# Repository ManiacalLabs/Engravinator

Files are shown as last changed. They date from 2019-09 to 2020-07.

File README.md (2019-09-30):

# Engravinator

The Engravinator is an Open Hardware laser engraver platform, designed to be robust and easy to build. It uses a combination of aluminum extrusions, commodity parts easily sourced from the 3D printer world, and 3D printed parts.

Unlike most laser engravers, however, it is designed to be brought to the work piece, not the other way around. It's compact and lightweight frame allows it to easily be rested, or even clamped, onto nearly any item you want to engrave.

Its existence is two-fold: To be both a fully functional laser engraver platform as designed *and* to be a highly flexible reference platform for other open designs.

For full details go to https://Engravinator.com

# Mk1 Specs

- 130mm x 130mm working area
- 345mm x 305mm x 245mm (W x D x H) overall size
- Under 4kg total weight at full spec
- Supports common PWM diode laser modules with a 16mm x 40mm M3 mounting pattern
- Up to 10,000 mm/min on X and 6,000 mm/min on Y travel speed
- 10 micron resolution (using 1/16 micro-stepping)
- 8mm linear rods and bearings on both axis
- Rigid 2020 aluminum extrusion frame
- Optional (but recommended!) full enclosure for maximum eye safety

# Design & License

As with all things from Maniacal Labs, the Engravinator is open hardware and is licensed under the [CERN Open Hardware License](/LICENSE).

You can find a complete [Fusion 360 archive](/Mk1/Engravinator.f3z) which contains the full design and all design history.

The [Fabrication](/Mk1/Fabrication/) directory contains a full set of exported files for everything you need to build the machine. For 3D Printed components we provide both `STL` files for printing and `STEP` files in case you would like to make modifications to a single model outside of the complete design, or in a different CAD tool.

# Mandatory Safety & Legal Warning

**Lasers are dangerous!** Seriously, we cannot stress enough that any laser, even low power lasers, if used improperly, can cause severe damage or injury. Use common sense and always use proper safety equipment.

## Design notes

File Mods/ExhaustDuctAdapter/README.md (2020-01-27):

# 4-Inch Exhaust Duct Adapter

Is the 80mm exhaust fan and carbon filter just not cutting it? No worries, just print this 4-inch duct adapter and vent outside!

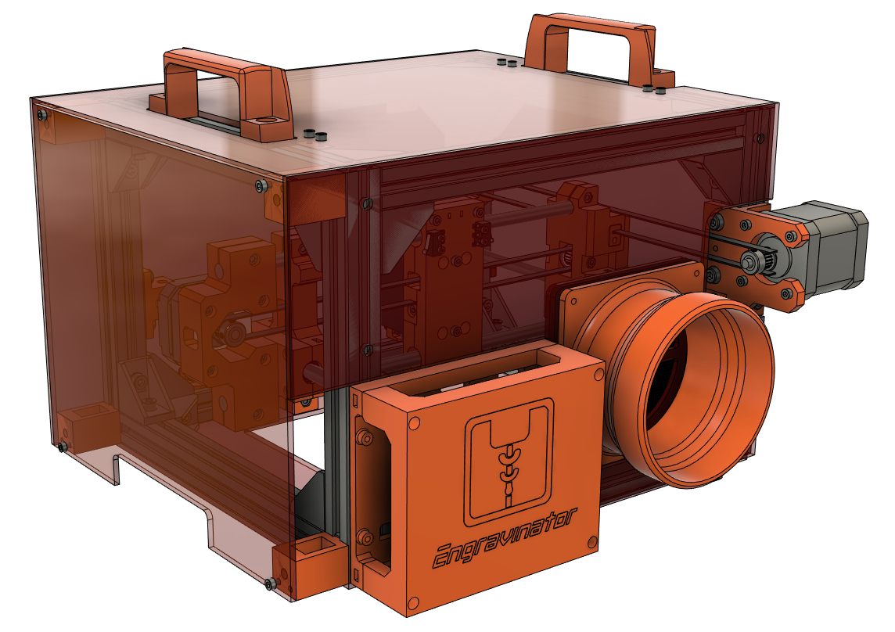
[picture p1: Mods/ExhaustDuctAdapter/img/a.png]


## Required Components

- Duct Adapter Printed Part - [4InchDuctAdapter.stl](4InchDuctAdapter.stl)
- 4x M3x10 bolts
- 4x M3 Nuts
- 4-inch flexible ducting
- 4-inch exhaust blower fan

## Assembly

- Print [4InchDuctAdapter.stl](4InchDuctAdapter.stl). We recommend 0.2mm layer heights with 20% infill. But it doesn't really matter.
- Remove the back panel from your Engravinator if it was already installed and remove the fan and filter holder.
- Use the M3x10 bolts and M3 nuts to mount the duct adapter to your Engravinator.
- Remount the back panel.

What, you were expecting more?

The rest is really up to you. We've had good luck with a generic 200CFM exhaust blower found on Amazon. Anything that's for a 4-inch duct hose will work. Connect one length of duct from the Engravinator to the blower (ideally using duct clamps but tape works too) then another length from the exhaust end of the blower to wherever you want to vent. Out a window works well.

If you are really stuck with no outside venting options we recommend using a large carbon filter canister such as this one: https://www.amazon.com/gp/product/B07B3RNW35/

This filter canister setup was used with great success for 2 solid days at ERRF 2019 with no complaints from anyone about fumes or smoke.

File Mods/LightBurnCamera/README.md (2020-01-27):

# LightBurn Camera

LightBurn has this [awesome feature](https://github.com/LightBurnSoftware/Documentation/blob/master/Using_a_Camera.md) that allows you to accurately place your designs using a calibrated camera view. Follow bellow to find out how to install a compatible camera on your Engravinator!

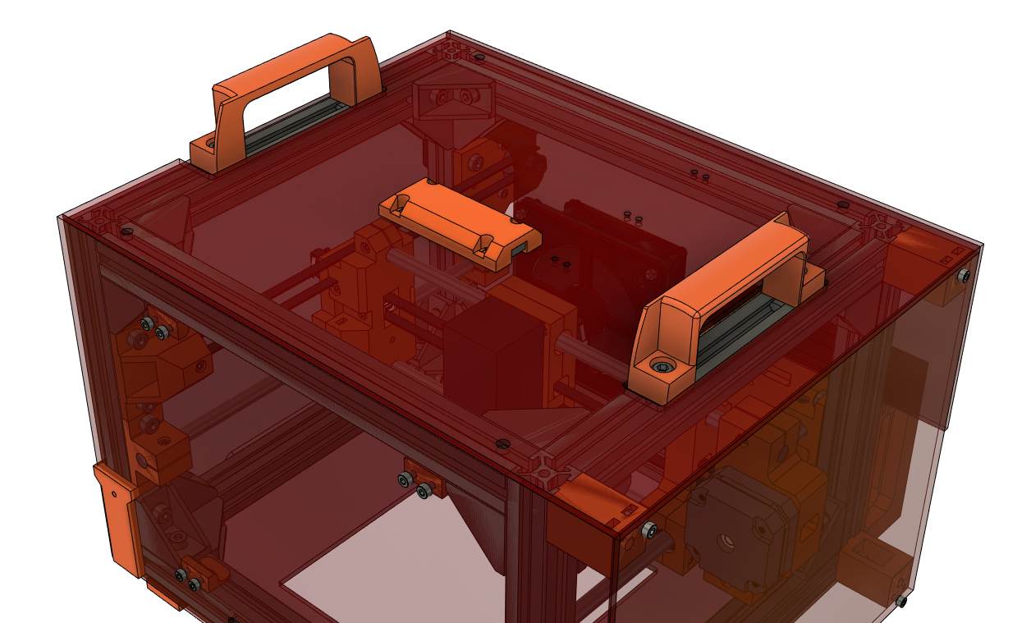
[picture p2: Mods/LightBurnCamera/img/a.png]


## Required Components

- Camera Mount (3D Printed) - [LightBurnCameraMount.stl](LightBurnCameraMount.stl)
- New top panel, cut from [TopPanel_LightBurnCamera.dxf](TopPanel_LightBurnCamera.dxf)  in 3mm 2422 Amber acrylic.
- [LightBurn Camera 90&deg;](https://lightburnsoftware.com/collections/cameras/products/lightburn-camera?variant=13886769922093)
- 2x M1.7x3mm Screws (or just use hot glue)
- 4x M3x10 bolts
- 4x M3 Nuts
- 4x M5x10 bolts
- 4x [HNTP5-5](https://us.misumi-ec.com/vona2/detail/110302247640/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) Spring nuts
- Small zip ties

## Assembly

This one is pretty simple:

- Before anything, there is a small dab of glue holding the camera lens at a specific focus. Pick that off with some small tweezers so we can focus it later.
- Print the camera mount listed above. 0.2mm layer heights, 20% infill.
- Mount the LightBurn camera in it with the M1.7 screws or, honestly, just use a couple dabs of hot glue. Those screws are a pain to find.
- Mount the camera mount to the new top acrylic panel using the M3x10 bolts and M3 nuts. See picture above for orientation.
- Connect the USB cable to the camera and hold it down using the 3 other sets of holes in the top panel and some zip ties.
- Mount the top panel to the frame using the M5x10 bolts and HNTP5-5 extrusion spring nuts. The top panel MUST be firmly mounted and not be allowed to shift at all.

That's it, not it just needs to be setup with LightBurn. All of the LightBurn camera docs can be found here: https://github.com/LightBurnSoftware/Documentation/blob/master/Using_a_Camera.md

One thing of note is that the lens calibration step requires a calibration pattern to be printed out and placed various places inside the machine. But it was never intended for a machine this small. We recommend printing out the calibration pattern at 25% size and then taping it to a small piece of stiff cardboard, roughly the size of a business card.

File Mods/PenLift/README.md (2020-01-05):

# Pen Lift Mechanism

So, maybe lasers aren't your thing and you prefer ink? Just install this pen lift mechanism that is a drop in replacement for the laser module :)

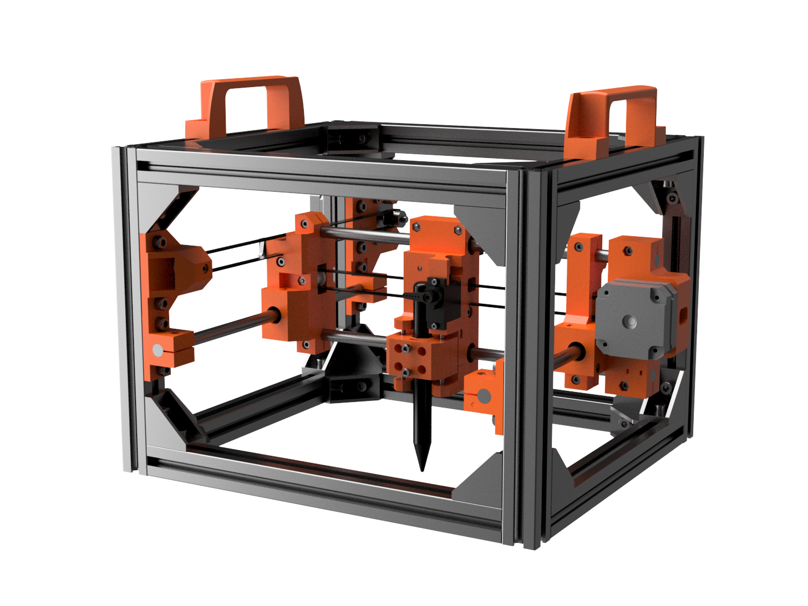
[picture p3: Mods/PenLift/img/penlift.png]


## Required Components

- Printed Components (Use [PenLiftPrintPlate.stl](Printed_Parts/PenLiftPrintPlate.stl))
- [9g Micro Servo](https://www.amazon.com/gp/product/B07NV476P7/)
- 4x [LMU3 Bearings](https://us.misumi-ec.com/vona2/detail/110300026540/?HissuCode=LMU3)
- 2x [3mm Diameter x 40mm linear rod](https://us.misumi-ec.com/vona2/detail/110302634310/?HissuCode=PSFJ3-40)
- 12x M3 Nut (See Engraviator [BOM Guide](https://engravinator.com/mk1/BOM_Guide.html))
- 2x [M3x10 Bolt](https://us.misumi-ec.com/vona2/detail/221000551286/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)
- 2x [M2x8 Bolt](https://us.misumi-ec.com/vona2/detail/221000551286/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)
- 6x [M3x15 Bolt](https://us.misumi-ec.com/vona2/detail/221000551286/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) (4 more will be reused from laser mount)
- Thin wire or fishing line
- Pen up to 12mm in diameter

## Assembly

This one is pretty simple, so in lieu of the full step-by-step we'll provide this annotated and exploded view of the entire assembly.

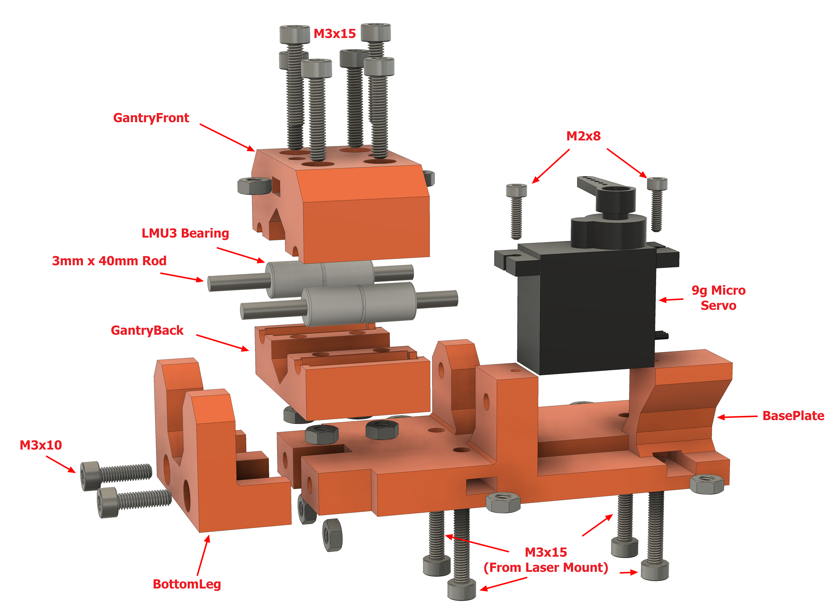
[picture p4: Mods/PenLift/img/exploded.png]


The basic steps are:

- Sandwich the four LMU3 bearings between `GantryFront` and `GantryBack`, then secure with four each of the M3x15 bolts and the M3 nuts. On GantryFront this is the 4 outer holes.
- Slide each of the 3mm rods into the bearings and then press the rods into the recessed holes on `BasePlate`.
- Take `BottomLeg` and match up the other ends of the rods with its recessed holes while lining it up with `BasePlate` and push them together as much as possible.
- Now insert two M3 nuts into the slots on the back of `BasePlate` and then two M3x10 bolts through the bottom of `BottomLeg` and tighten against those nuts. This will pull everything together and fully seat the 3mm rods.
- In `GantryFront` there are two slots for M3 nuts. Insert a nut into each and then thread in an M3x15 bolt from the top for each. These are to hold onto the pen, so do not tighten all the way yet.
- Use the M2x8 bolts to secure the micro servo.
- We recommend installing a single servo arm as shown. We will discuss connecting this to the gantry in the usage details below.

## Mounting

The pen lift mechanism goes in place of the laser.

- Simply undo the four M3x15 bolts on the back of the X-axis laser mount but leave the bolts in place. Just remove the laser. 
- Then insert an M3 nut into each of the 4 slots on the side of `BasePlate`.
- Mount the pen lift on the X-axis, matching up the holes with those M3x15 bolts. Tighten all bolts to secure.
- Finally you will need to run the servo cable in place of (or along side) the laser cable back to the controller. See the [Controller section](https://engravinator.com/mk1/build/06.Controller.html) of the build guide for more details on wiring.

## Firmware

Unfortunately it's not possible to just use stock Grbl to control a servo. There are two types of modified Grbl to control this mechanism. One controls the servo with the laser power commands and the other controls the servo as a virtual Z axis. We will be only discussing the former here. You can find firmware that uses the latter on this [GitHub repo])(https://github.com/bdring/Grbl_Pen_Servo).

However, for the Engravinator we recommend you use the firmware that we have created, which is been thoroughly tested and will be detailed here. Note: we will be assuming you are using the [Platypus](https://maniacallabs.com/products/platypus/) controller below.

First, follow the instructions here: https://github.com/ManiacalLabs/grbl/tree/builds
And install the firmware called `m3_servo`:

- [Precompiled Hex](https://github.com/ManiacalLabs/grbl/tree/builds/release/m3_servo)
- [Source](https://github.com/ManiacalLabs/grbl/tree/builds/code/m3_servo)

You will then need to change a few config items. Enter these commands (without the comment) in your controller serial terminal.

- Disable laser mode `$32=0`
- Decrease default X speed: `$110=2000.000`
- Decrease default Y speed: `$111=2000.000`

You **MUST** disable laser mode, otherwise it will move with the pen down when it shouldn't. The last two are optional but you really don't want to be going fast with a pen. This will limit it for you.

That's it, your controller is ready to rock a servo!

## Pen Setup

Almost there, we promise! The first thing we need to do is get the pen installed and hook up the servo to the gantry. 

With your Engravinator on, connected to your control software of choice, and homed: open your serial terminal and enter: 

`M3 S0`

This will move the servo to the "neutral position". At this point, make sure the servo arm is pointing to "9 o'clock" as shown in the picture below: 

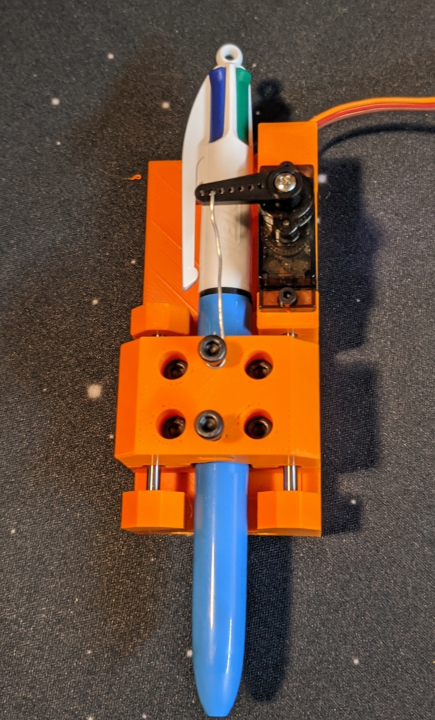
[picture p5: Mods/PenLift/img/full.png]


If the arm is not in that position, unscrew it and move it to the correct position before screwing it in again.
With the arm there, take either a piece of ~22 gauge wire (without the insulation) or some fishing line and connect it between the servo arm and the top bolt as shown above. Using fishing line will provide no downward pressure whereas a wire will provide a little. We prefer the wire because it will also bend a bit if the servo moves down too far and basically "auto adjust".

Now, enter the command:

`M3 S250`

This will move the arm to about 1/4 of full. You might think you'd want to fully extend it but that's not the case. Ideally the pen should only move up and down a tiny amount, which allows you to spend less time deploying and stowing the pen.

Now, loosen the two bolts in the center of the gantry and insert your pen of choice from the top (without the cap of course). Let it simply rest on the surface below your Engravinator. Tighten both bolts so that it holds the pen securely.

Now enter `M5` in the terminal to "stow" the pen.

## Control

This will be a little different depending on what software you choose. But no matter what you'll need to ensure that you have it program in a delay for every `M3` (pen down) command. The easiest way to do this is with the `G4` (dwell) command.

Some programs, such as LaserWeb will allow you to set "Tool On" and "Tool Off" commands. In this case, you would use:

```
; tool on
M3 S250
G4 P250

; tool off
M5
G4 P100
```

Note that the `Sxxx` value must be whatever you used above to setup your pen. Because that's where your pen is touching the paper.

The `G4 Pxxx` values are a delay where the number is milliseconds. In our testing we've found that 250ms is usually enough to make sure the pen is fully deployed and 100ms is enough to ensure it's no longer touching the surface before moving again.

These values will change depending on your particular usage. For example, if you notice that it's skipping part of a line after deploying the pen, increase the tool on delay. Or if you see that it's drawing after it should've stopped, increase the tool off delay. The idea is to have those values be as small as possible, as to not waste time.

That's pretty much it, assuming your software let's you override tool on / tool off or otherwise set delays. Now you can use it just like you would for a laser.

## LightBurn

We really love [LightBurn](https://lightburnsoftware.com) here at Maniacal Labs for all our lasering needs, but for pen use it requires a few tweaks. Mainly this is because there's currently no way to override the tool on/off commands as described above. But no worries, it's an easy fix.

First, you need to make sure that it won't use M4 power commands which means using a different GRBL profile than then one described in the [Platypus LightBurn docs](https://github.com/ManiacalLabs/Platypus/blob/master/docs/LightBurn.md). At this point we recommend creating a completely new profile to be used with the pen lift. Follow those LightBurn docs for the Platypus but when it asks you to choose a laser type, choose `GRBL-M3 (1.1e or earlier)`:

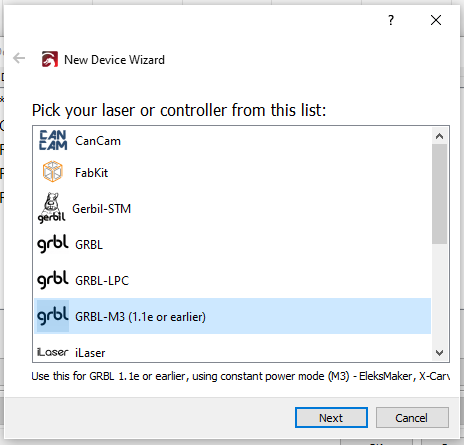
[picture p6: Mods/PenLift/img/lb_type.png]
lightburn type


Follow the rest of the Platypus docs and use all the same options otherwise. Now you just need to ensure there's a delay on pen down/up. In your cut settings you need to enable the "Cut Through" mode, as shown below:

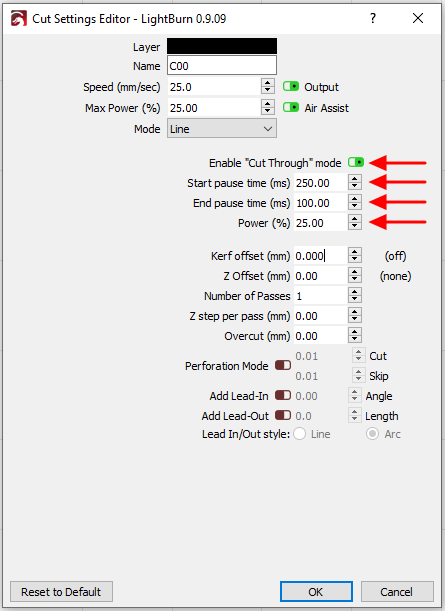
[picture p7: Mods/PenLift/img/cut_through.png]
Cut Through


The four annotated items are what's imported. 

- "Cut Through" must be turned on
- "Start pause time" is the delay on pen down
- "End pause time" is the delay on pen up
- "Power" should always be whatever "Max Power" at the top of the dialog is set to. Unfortunately you always have to set both and make sure they are the same.

Since power is in percent in LightBurn, note that 25% here is the same as `S250` above, assuming that your power range is configured for 0-1000 in Grbl (the default).

One thing we've found is that you can increase the power setting a little bit from what you used when installing the pen to provide a little more pressure (assuming you used wire instead of fishing line). So, for example, set it to 30% when the pen was installed at 25%.

That's it! You should be good to go with LightBurn.

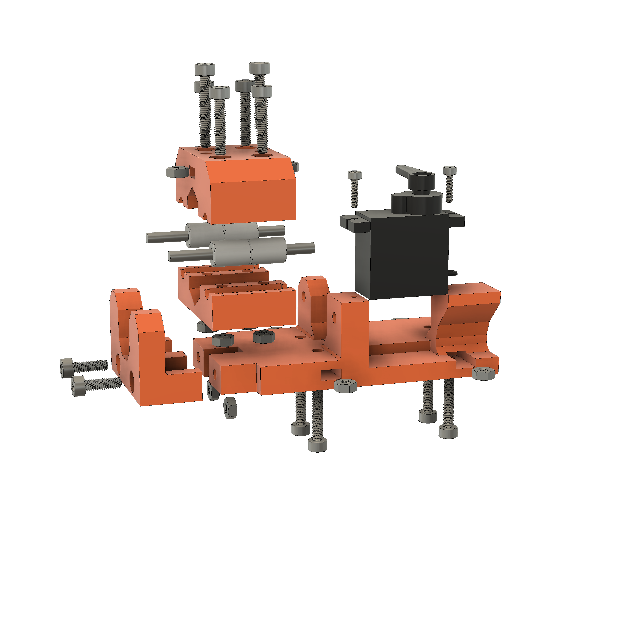
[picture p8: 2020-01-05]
Mods/PenLift/img/a.png

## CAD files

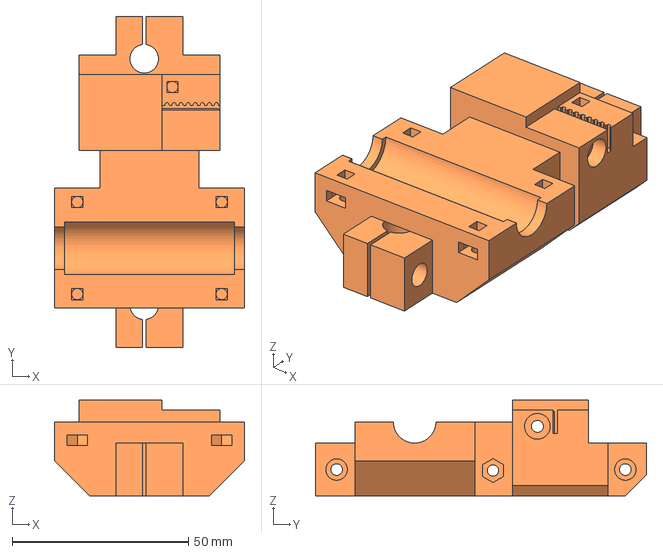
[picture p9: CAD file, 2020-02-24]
Mk1/Fabrication/3D_Printed/Core_Components/Y_Drive_Main.step
54.0 x 94.0 x 27.2 mm

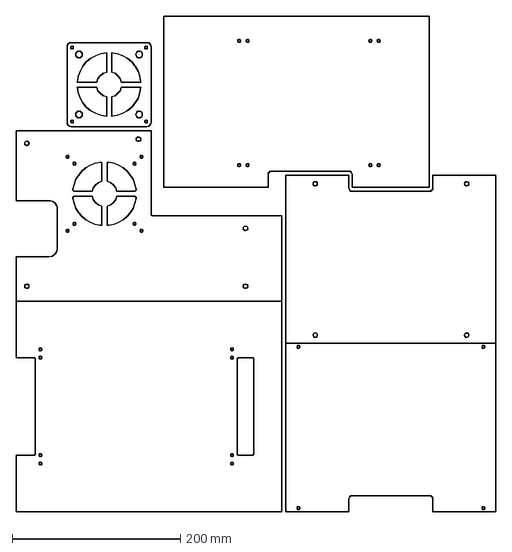
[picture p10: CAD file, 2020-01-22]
Mk1/Fabrication/Laser_Cut/ProductionFiles/FullPanelCut_SharedBorders.dxf
571.0 x 589.0 mm

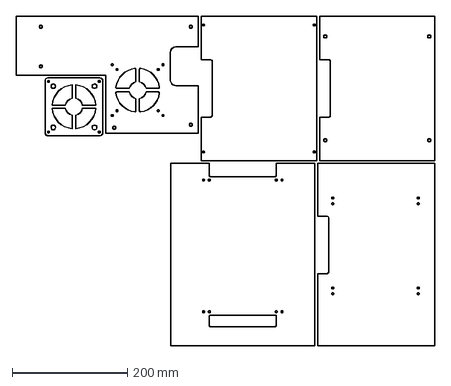
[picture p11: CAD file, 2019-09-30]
Mk1/Fabrication/Laser_Cut/FullPanelCut.dxf
726.0 x 571.0 mm

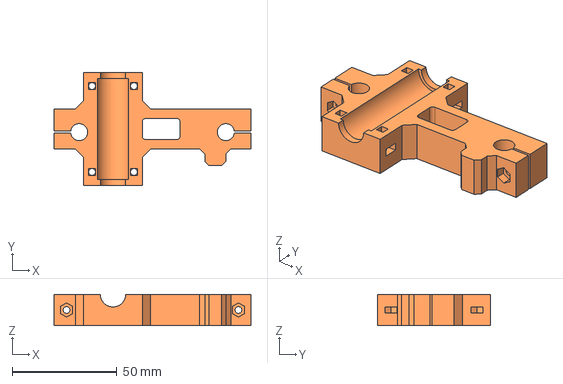
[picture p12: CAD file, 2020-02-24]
Mk1/Fabrication/3D_Printed/Core_Components/Y_Idle_Main.step
94.0 x 54.0 x 15.0 mm

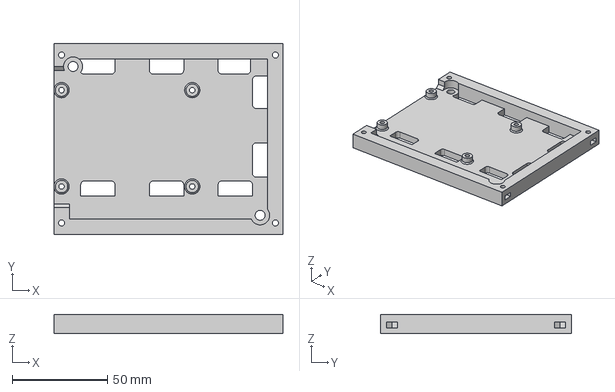
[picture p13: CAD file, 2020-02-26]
Mk1/Fabrication/3D_Printed/Controller_Box/BasePlate_Platypus.step
120.0 x 100.0 x 10.0 mm

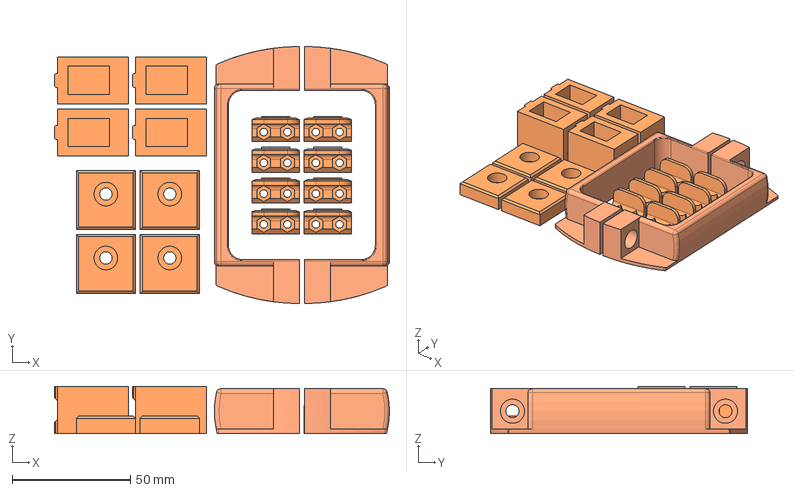
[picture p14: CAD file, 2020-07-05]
Mk1/Fabrication/3D_Printed/Enclosure/EnclosurePrintPlate.step
141.5 x 108.5 x 20.0 mm
x2_Handles x 2
x4_Feet x 4
x4_ExtensionBracket x 4
x8_PanelClips x 8

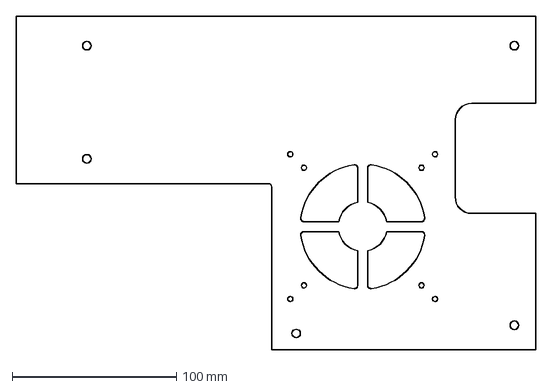
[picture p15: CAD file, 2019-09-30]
Mk1/Fabrication/Laser_Cut/BackPanel.dxf
316.0 x 203.0 mm

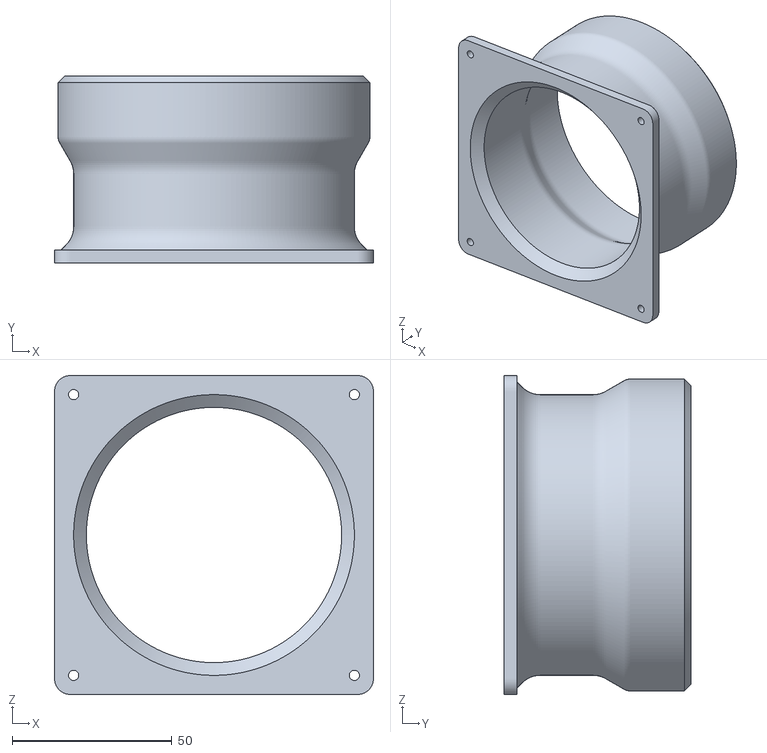
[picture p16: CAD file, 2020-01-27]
Mods/ExhaustDuctAdapter/4InchDuctAdapter.stl
100.0 x 58.5 x 100.0

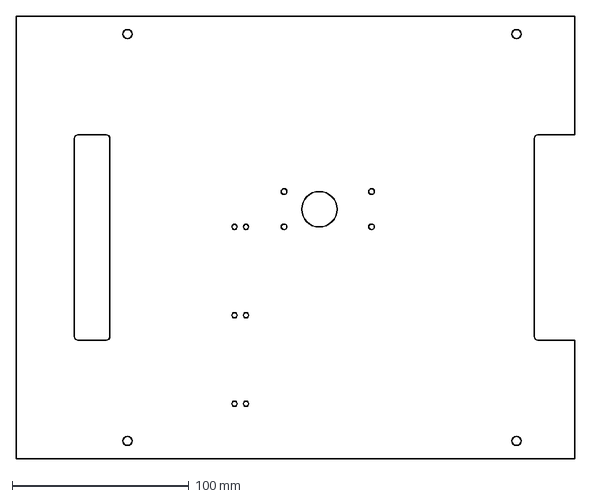
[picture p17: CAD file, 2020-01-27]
Mods/LightBurnCamera/TopPanel_LightBurnCamera.dxf
316.0 x 250.0 mm

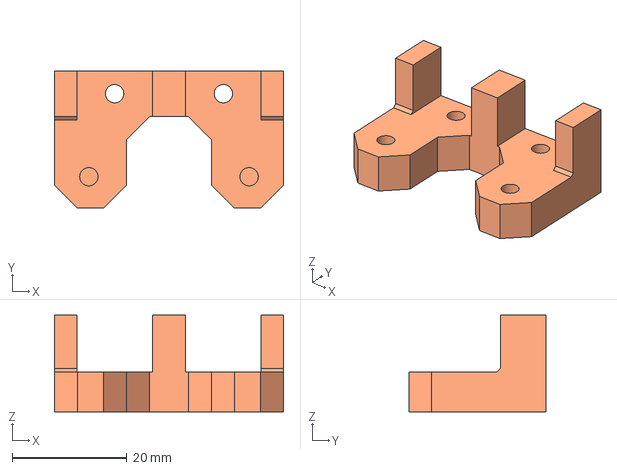
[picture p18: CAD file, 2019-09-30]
Mods/PenLift/Printed_Parts/BottomLeg.step
40.0 x 24.0 x 16.9 mm

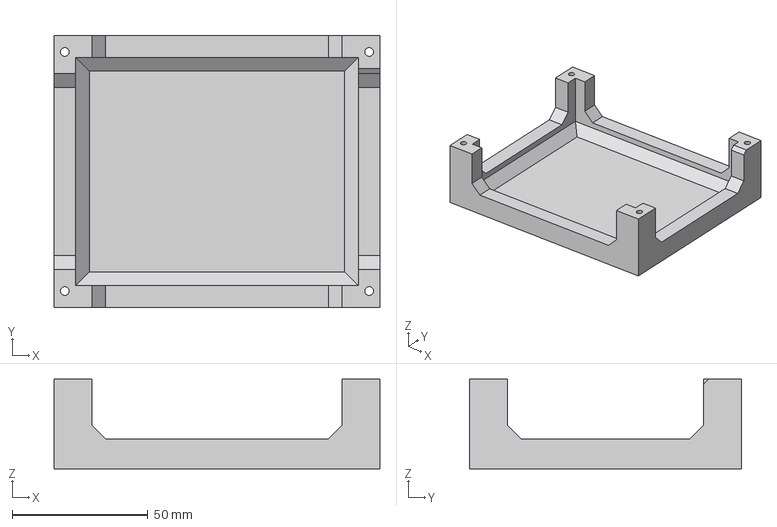
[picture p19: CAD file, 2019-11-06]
Mk1/Fabrication/3D_Printed/Controller_Box/ControllerCover_NoLogo.step
120.0 x 100.0 x 33.0 mm

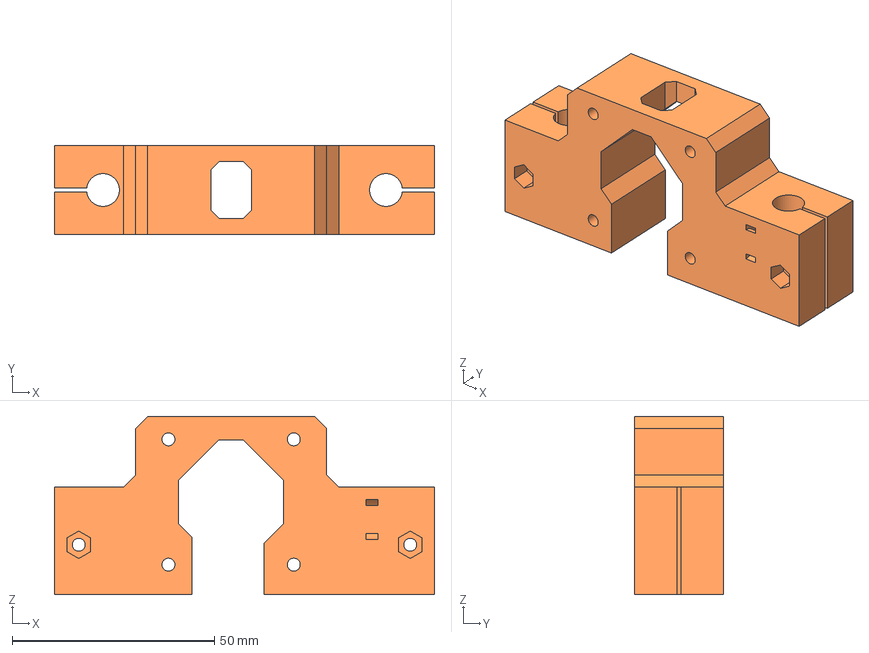
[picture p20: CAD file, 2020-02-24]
Mk1/Fabrication/3D_Printed/Core_Components/X_Motor_Mount.step
94.0 x 22.0 x 44.1 mm

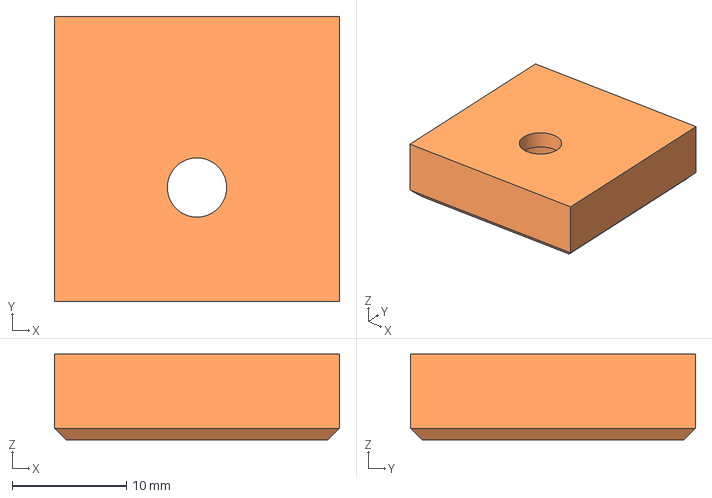
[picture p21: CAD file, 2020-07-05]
Mk1/Fabrication/3D_Printed/Enclosure/x4_Feet.step
25.0 x 25.0 x 7.50 mm

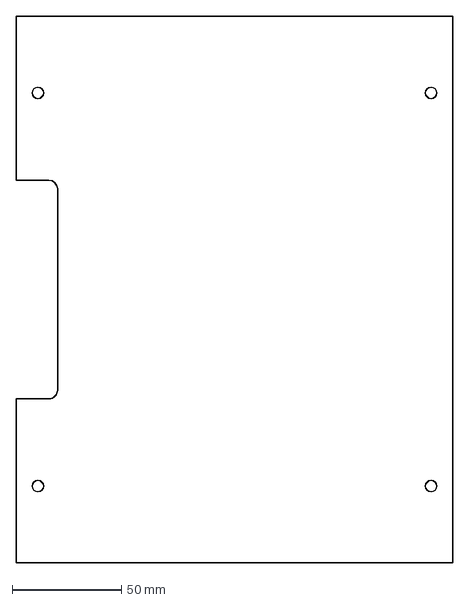
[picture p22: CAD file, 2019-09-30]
Mk1/Fabrication/Laser_Cut/LeftPanel.dxf
200.0 x 250.0 mm

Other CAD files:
Mods/LightBurnCamera/LightBurnCameraMount.stl
Mods/PenLift/Printed_Parts/GantryBack.step
Mk1/Fabrication/3D_Printed/Controller_Box/CorePrintPlate.step
Mk1/Fabrication/3D_Printed/Core_Components/X_Back_Plate.step
Mk1/Fabrication/3D_Printed/Controller_Box/BasePlate_BartDring_PenLaserController v2.step
Mk1/Fabrication/3D_Printed/Controller_Box/BasePlate_BartDring_PenLaserController.stl
Mk1/Fabrication/3D_Printed/Controller_Box/BasePlate_Platypus.stl
Mk1/Fabrication/3D_Printed/Controller_Box/ControllerCover.step
Mk1/Fabrication/3D_Printed/Controller_Box/ControllerCover.stl
Mk1/Fabrication/3D_Printed/Controller_Box/ControllerCover_NoLogo.stl
Mk1/Fabrication/3D_Printed/Core_Components/HeightTool.step
Mk1/Fabrication/3D_Printed/Core_Components/HeightTool.stl
Mk1/Fabrication/3D_Printed/Core_Components/MiniPlate_1.stl
Mk1/Fabrication/3D_Printed/Core_Components/MiniPlate_2.stl
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

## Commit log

2019-08-30 Added Mk1 fabrication files
    [BackPanel.dxf, BasePlate_BartDring_PenLaserController v2.step, BasePlate_BartDring_PenLaserController.stl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]
2019-08-30 added rod holder model
    [x4_RodHolder.step, x4_RodHolder.stl]
2019-08-30 Update Platypus controller mount
    [BasePlate_Platypus.step, BasePlate_Platypus.stl]
2019-09-02 Update fab docs and add F360 archive
    [EnclosurePrintPlate.step, EnclosurePrintPlate.stl, x4_Feet.step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]
2019-09-07 Update fab files
    [BasePlate_Platypus.step, BasePlate_Platypus.stl, EnclosurePrintPlate.step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]
2019-09-12 update tensioners, starting pen lift
    [BasePlate.stl, BottomLeg.stl, GantryBack.stl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]
2019-09-30 Updating 3D models
    [4InchDuctAdapter.stl, BackPanel.dxf, BasePlate.step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]
2019-11-06 Adding logo-less controller cover
    [ControllerCover_NoLogo.step, ControllerCover_NoLogo.stl]
2019-11-08 Update enclosure print plate
    [EnclosurePrintPlate.step, EnclosurePrintPlate.stl]
2019-11-13 Fixing rod compression components
    [CorePrintPlate.step, X_Motor_Mount.step, X_Motor_Mount.stl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]
2019-12-05 Fixing core print plate to be more compact
    [CorePrintPlate.step]
2020-01-05 remove duct adapter
    [4InchDuctAdapter.stl]
2020-01-05 Add pen lift mod
    [BasePlate.step, BasePlate.stl, BottomLeg.step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]
2020-01-22 Add production files for enclosure
    [FullPanelCut_SharedBorders.dxf]
2020-01-27 Adding lightburn camera mod
    [LightBurnCameraMount.stl, TopPanel_LightBurnCamera.dxf]
2020-01-27 Adding duct adapter mod
    [4InchDuctAdapter.stl]
2020-02-24 updating model files
    [CorePrintPlate.step, MiniPlate_1.stl, MiniPlate_2.stl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]
2020-02-26 Update controller base plate
    [BasePlate_Platypus.step, BasePlate_Platypus.stl]
2020-07-05 Update models with 10mm hole in feet
    [EnclosurePrintPlate.step, EnclosurePrintPlate.stl, x4_Feet.step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]
